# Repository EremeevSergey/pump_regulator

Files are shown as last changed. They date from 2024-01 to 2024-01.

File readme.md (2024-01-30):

# Реле контроля уровня.
## Описание.

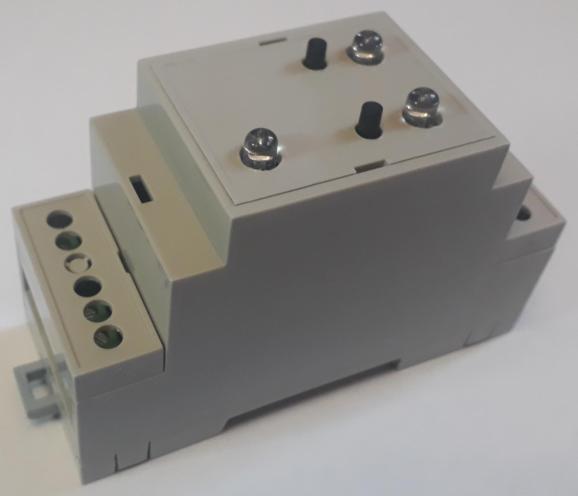
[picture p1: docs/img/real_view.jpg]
Внешний вид


Позволяет контролировать уровень жидкости (откачивать/закачивать). Для контроля используются датчики с ***сухим контактом***, например:

+ [Датчик уровня жидкости герконовый](https://market.yandex.ru/product--poplavkovyi-vykliuchatel-priamoi/1811578569?sku=101921281993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)
+ [Поплавковый герконовый датчик уровня воды](https://www.ozon.ru/product/liquid-level-switch-m15-poplavkovyy-gerkonovyy-datchik-urovnya-vody-zhidkosti-rezba-m15-kabel-688831200/)
+ [Поплавковый выключатель, контроль уровня воды]( https://market.yandex.ru/product--poplavkovyi-vykliuchatel-priamoi/1811578569?sku=101921281993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)

Можно использовать нормально разомкнутые, нормально замкнутые контакты, а также и те и другие одновременно  (программируется каждый контакт индивидуально). Выход Реле имеет контакт нормально-замкнутый и нормально-разомкнутые контакты. 

Изначально Реле (устройство) разрабатывалось для откачки воды, но оно может быть использовано и для наполнения воды.

## Органы управления и индикации.
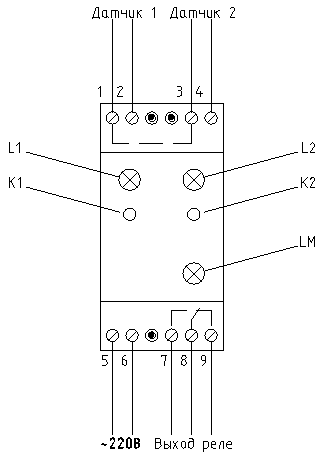
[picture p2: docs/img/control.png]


**Назначение клемм указано на рисунке.** Следует отметить, что клеммы 1, 3 внутри соединены между собой.

**L1, L2 - светодиоды, показывающие состояния датчиков (1 и 2 соответственно)**

| Цвет светодиода  | Описание |
|---|---|
| Красный | Датчик сработал |
| Зеленый | Датчик не сработал (контакт нормально-разомкнутый), т.е. контакт разомкнут.|
| Синий | Датчик не сработал (контакт нормально-замкнутые), т.е. контакт замкнут |

**K1, K2 - кнопки управления**

Долгое нажатие (10 сек. и дольше) на одну из кнопок переключает тип датчика с нормально-разомкнутого на нормально-замкнутый и наоборот. Тип датчика сохраняется даже после отключения питания. Для нормально-разомкнутого контакта в несработанном состоянии светодиод горит Зеленым цветом, а для нормально-замкнутого - Синим.

Если нажать и удерживать (10 сек. и дольше) одновременно две кнопки, то Реле переключиться с автоматического на ручной режима работы (и наоборот).
При переходе в ручной режим работы выход Реле отключается. Режим работы не запоминается и при включении, всегда устанавливается автоматический режим.

В ручном режиме работы кнопка K1 включает выходное Реле, а кнопка K2 - выключает. Для возврата в автоматический режим надо либо отключить питание (секунды на 2-3) либо нажать и удерживать (10 сек. и дольше) одновременно две кнопки K1 и K2. 

**LM - светодиод состояния выходного реле**
| Цвет светодиода  | Описание |
|---|---|
| Красный горит | Выходного реле включено |
| Зеленый горит | Выходного реле (автоматический режим работы) |
| Синий горит | Выходного реле (ручной режим работы) |

Если светодиод моргает (не важно каким цветом), значит Реле не смогло правильно прочитать из внутренней памяти (или записать в память) тип датчика. В этом случае тип всех контактов всегда будет нормально-разомкнутым. Вообще такое вряд-ли может случиться, т.к. ресурс флэш-памяти микроконтроллера реле позволят записывать не менее 100 000 раз. Чтобы затереть ячейки флэш-памяти надо будет очень часто менять типы контактов датчиков.

## Подключение.
### Откачиваем воду.
Схема подключения приведена ниже.
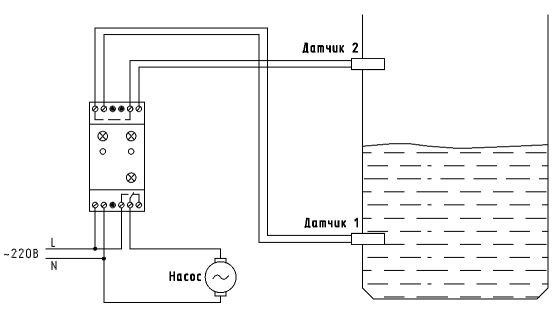
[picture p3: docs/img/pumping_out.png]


Самый правильный вариант, это поставить нормально-разомкнутые контакты (Датчик 1 и Датчик 2). В данном случае насос будет включаться только когда уровень воды поднимется выше Датчика 2 и будет откачивать воду пока её уровень не опустится ниже Датчика 1, или пропадёт напряжение питания (после восстановления питания, откачка воды возобновиться только, когда уровень воды опять поднимется выше датчика 2).

Если нет нормально-разомкнутых датчиков, можно поставить и нормально-замкнутые. В это случае надо будет кнопками К1, К2 поменять тип датчика (см. выше). 

### Набираем воду.

Как упоминалось в начале, Реле изначально разрабатывалось для откачки воды. Поэтому для обеспечения наборы воды есть несколько вариантов, каждый из которых имеет нюансы:

1. Назовём этот вариант "агрессивный". Т.е., если при включении  уровень воды будет ниже Датчика 2, насос включится и будет работать пока не "докачает" воду до Датчика 2. Далее он выключиться до тех пор пока уровень воды не спадёт до уровня Датчика 1. 

Подключение аналогично схеме "откачки воды", только насос подключаем к замкнутому выходному контакту Реле а не к разомкнутому.

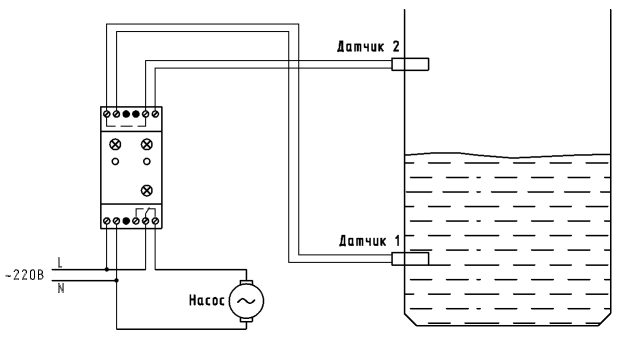
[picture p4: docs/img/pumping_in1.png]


Этот вариант меня смущает тем, что мы подключаем насос к нормально-замкнутым выходным контактам (см. схему). Вроде и ничего, но .... а вдруг Реле "сдохнет". Тогда с большей вероятностью выход отключиться, но т.к. насос подключен к нормаль-замкнутым контактам, он будет работать, пока мы его из сети не выключим.

2. Назовём это вариант "ленивый".
В данном варианте мы меняем местами датчики, и кнопками "инвертируем" состояния датчиков (программируем, см. выше), т.е. если у нас стоят нормально-разомкнутые контакты, мы их переводим в режим нормально-замкнутых, и наоборот. Насос подключаем через нормально-разомкнутые контакты Реле (как и при откачки воды).

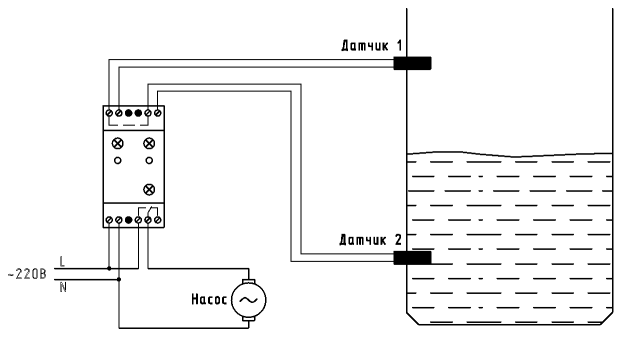
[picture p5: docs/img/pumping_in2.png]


При такой схеме включения насос будет включаться только, если уровень воды опуститься ниже Датчика 2, и работать до тех пор, пока уровень воды не достигнет Датчика 1. Здесь у нас нет минуса первого варианта, но то, что мы меняем тип контакта, возможно может сбить с толку. Мне данный вариант кажется более надежным и оптимальным.

[Кое-что про изготовление](docs/build.md)

[Для тех, кто будет переделывать (дорабатывать)](docs/info.md)

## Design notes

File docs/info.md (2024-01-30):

# Для тех, кто решит что-либо переделать.
## Программы

Я использовал:
1. [Kicad](https://www.kicad.org/download/) для разработки схем и печатных плат.
2. [Eclipse](https://www.eclipse.org/downloads/packages/release/2023-12/r/eclipse-ide-embedded-cc-developers) для отладки (разработки) прошивки микроконтроллера
3. [OpenOCD](https://github.com/openocd-org/openocd/releases/download/v0.12.0/openocd-v0.12.0-i686-w64-mingw32.tar.gz)  для программирование микроконтроллера и отладки
4. Qt Creator  и Qt 5.15.XX для написания эмулятора насосной станции и основной части прошивки (не зависящей от используемого микроконтроллера, да и системы вообще).

Думаю для пользователей Linux-ов не возникнет проблем с установкой этих программ. В Debian я всё за исключением Eclipse устанавливал пакетным менеджером. Eclipse скачивал с официального сайта.

А вот пользователи Windows могут столкнутся с проблемами при скачивании Qt Creator  и Qt 5.15.XX. Нехорошие люди не дают скачивать инсталяторы с официального сайта Россиянам. Мне не помогли даже танцы с бубном... Но если не использовать эмулятор, то и не надо будет всё это скачивать.

## Структура каталогов
```
./
 +-- case                      - документация на корпус
 +-- docs                      - то что мы сейчас читаем
 +-- firmware                  - проект Eclipse прошивки микроконтроллера
 |   +-- release/stm32f030f4p6 - сама прошивка
 |   +-- src/system            - не зависимый от платформы исходный код прошивки
 |   |   +-- config.h          - настроечные константы прошивки
 |   |   +-- hw_specific.h     - предварительные объявления функций, зависящих от платформы
 |   |   |   ...
 |   |      
 |   +-- stm32f030f4p6         - код пошивки для MCU stm32f030f4p6
 |       +-- eeprom            - "драйвер" виртуального EEPROM
 |       |   ...               - всё, что касается stm32f030f4p6
 |       
 +-- kicad
 |   +-- mcu/stm32f030f4p6     - проект Kicad платы микроконтроллера
 |   +-- power                 - проект Kicad силовой платы 
 |
 +-- simulator                 - прокт Qt Creator эмулятора
 ```
 
## Железо
Я использую Kicad, т.к. я нищеброд, и денег на платный софт у меня нет. А Kicad перекрывает все мои потребности, бесплатный, развивающийся и работает на всех системах (Linux, Windows, macOS).

Проекты Kicad-а лежат в отдельных папках  [Силовая плата](../kicad/power/), [Плата микроконтроллера](../kicad/mcu/stm32f030f4p6/)

## Прошивка
Основной код системы лежит в [firmware/src/system/](../firmware/src/system/). Он же используется и в эмуляторе, т.е. его напрямую там можно отладить. 

Файл "config.h" содержит настроечные константы (делители для таймеров) а также описаны используемые ножки микроконтроллера. Файл "hw_specific.h" содержит объявления функция зависящих от оборудования. Определения этих функций содержатся для stm32f030f4p6 в [hw_specific.cpp](../firmware/stm32f030f4p6/hw_specific.cpp), а для эмулятора в [simulator.cpp](../simulator/simulator.cpp).

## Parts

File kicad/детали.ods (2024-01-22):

Collated Components:
Item | Qty | Reference(s) | Value | LibPart | Цена | Стоимость | Магазин |  | Цена | Стоимость | Магазин
1 | 1 | BD1 | MB10F | диоды:MB10F | 4 | 4 | https://www.chipdip.ru/product/mb10f-hottech |  | 4 | 4 | https://www.chipdip.ru/product/mb10f-hottech
2 | 1 | C1 | C_Polarized_Small | Device:C_Polarized_Small | 18 | 18 | https://www.chipdip.ru/product0/9000565948 |  | 64 | 64 | https://www.chipdip.ru/product0/9000565948
3 | 1 | D1 | M3 | Device:D | 4 | 4 | https://www.chipdip.ru/product/m3-sunmate |  | 4 | 4 | https://www.chipdip.ru/product/m3-sunmate
4 | 1 | J1 | Conn_01x05 | Connector_Generic:Conn_01x05 | 2,6 | 2,6 | https://aliexpress.ru/item/32701800317.html?sku_id=61026197686 |  | 2,6 | 2,6 | https://aliexpress.ru/item/32701800317.html?sku_id=61026197686
5 | 1 | K1 | Реле_2-3 | реле:Реле_2-3 | 37 | 37 | https://aliexpress.ru/item/1005001994042589.html?sku_id=12000036214239182 |  | 42 | 42 | https://www.chipdip.ru/product0/8003916358
6 | 3 | P1, P3, P4 | CONN_2 | разъемы:CONN_2 | 12,7 | 38,1 | https://aliexpress.ru/item/32979388954.html?sku_id=66712511350 |  | 12,7 | 38,1 | https://aliexpress.ru/item/32979388954.html?sku_id=66712511350
7 | 1 | P2 | CONN_3 | разъемы:CONN_3 | 14,1 | 14,1 | https://aliexpress.ru/item/32979388954.html?sku_id=66712511351 |  | 14,1 | 14,1 | https://aliexpress.ru/item/32979388954.html?sku_id=66712511351
8 | 1 | T1 | Transformer_1P_1S | Device:Transformer_1P_1S | 540 | 540 | https://www.chipdip.ru/product0/8010765635 | https://www.chipdip.ru/product/tp112-k56 | 550 | 550 | https://www.chipdip.ru/product/tp112-k56
 | 1 | Печатная плата |  | (10 шт) | 290 | 290 |  |  | 600 | 600
Item | Qty | Reference(s) | Value | LibPart
1 | 2 | C1, C2 | C | Device:C | 2 | 4 |  |  |  | 0
2 | 1 | C3 | C_Polarized | Device:C_Polarized | 2 | 2 |  |  |  | 0
3 | 3 | D1, D2, D3 | LED_RKGB | Device:LED_RKGB | 8,8 | 26,4 | https://aliexpress.ru/item/32601543257.html?sku_id=65508728438 |  | 80 | 240 | https://www.chipdip.ru/product0/8413660661
4 | 1 | J1 | Conn_01x05 | Connector_Generic:Conn_01x05 | 2,6 | 2,6 | https://aliexpress.ru/item/32701800317.html?sku_id=61026197686 |  | 2,6 | 2,6 | https://aliexpress.ru/item/32701800317.html?sku_id=61026197686
5 | 1 | J2 | Conn_01x04 | Connector_Generic:Conn_01x04 | 2 | 2 | https://aliexpress.ru/item/32701800317.html?sku_id=61026197685 |  | 2 | 2 | https://aliexpress.ru/item/32701800317.html?sku_id=61026197685
6 | 2 | PB1, PB2 | кнопка | кнопки:кнопка | 6,05 | 12,1 | https://aliexpress.ru/item/1005004254514071.html?sku_id=12000028534796959 |  | 9 | 18 | https://www.chipdip.ru/product/kls7-ts6601-11.0-180-it-1102k
7 | 1 | Q1 | BC817 | Device:Q_NPN_BEC | 4 | 4 | https://www.chipdip.ru/product/bc817-16-hottech |  | 4 | 4 | https://www.chipdip.ru/product/bc817-16-hottech
8 | 1 | R1 | R | Device:R | 0,5 | 0,5 | https://aliexpress.ru/item/1005001794416354.html?sku_id=12000017596091305 |  | 0,5 | 0,5 | https://aliexpress.ru/item/1005001794416354.html?sku_id=12000017596091305
9 | 3 | R2, R5, R8 | 104 | Device:R | 0,5 | 1,5 | https://aliexpress.ru/item/1005001794416354.html?sku_id=12000017596091305 |  | 0,5 | 1,5 | https://aliexpress.ru/item/1005001794416354.html?sku_id=12000017596091305
10 | 4 | R3, R6, R9, R10 | 224 | Device:R | 0,5 | 2 | https://aliexpress.ru/item/1005001794416354.html?sku_id=12000017596091305 |  | 0,5 | 2 | https://aliexpress.ru/item/1005001794416354.html?sku_id=12000017596091305
11 | 2 | R4, R7 | 64 | Device:R | 0,5 | 1 | https://aliexpress.ru/item/1005001794416354.html?sku_id=12000017596091305 |  | 0,5 | 1 | https://aliexpress.ru/item/1005001794416354.html?sku_id=12000017596091305
12 | 1 | U1 | AMS1117-3.3 | Regulator_Linear:AMS1117-3.3 | 9 | 9 | https://www.chipdip.ru/product/ams1117-3.3-umw |  | 9 | 9 | https://www.chipdip.ru/product/ams1117-3.3-umw
13 | 1 | U2 | STM32F030F4Px | MCU_ST_STM32F0:STM32F030F4Px | 60,4 | 60,4 | https://aliexpress.ru/item/1005005652086561.html?sku_id=12000033892723179 |  | 190 | 190 | https://www.chipdip.ru/product/stm32f030f4p6
 | 1 | Печатная плата |  | (10 шт) | 338 | 338 |  |  | 600 | 600
 | 2 | Conn_01x05 | Мама |  | 1,6 | 3,2 | https://aliexpress.ru/item/32715864245.html?sku_id=61026413131 |  | 1,6 | 3,2 | https://aliexpress.ru/item/32715864245.html?sku_id=61026413131
 | 10 | Conn_01x05 | Контакты |  | 1,4 | 14 | https://aliexpress.ru/item/32690584570.html?sku_id=60493826630 |  | 1,4 | 14 | https://aliexpress.ru/item/32690584570.html?sku_id=60493826630
 | 1 | Корпус |  |  | 310 | 310 | https://meandr-shop.ru/korpus-141/ |  | 540 | 540 | https://www.chipdip.ru/product/d3mg
 |  |  |  |  |  | 1740,5 |  |  |  | 2946,6

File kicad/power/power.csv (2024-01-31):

Item | Qty | Reference(s) | Value | LibPart | Footprint | Datasheet | Qty | ChipDip | Цена | Стоимость | Aliexpress | Цена2 | Стоимость
1 | 1 | BD1 | MB10F | диоды:MB10F | диоды:MB-F |  | 1 | https://www.chipdip.ru/product/mb10f-hottech | 4 | 4 | https://aliexpress.ru/item/1005002106188652.html?sku_id=12000018760217218 | 4 | 4
2 | 1 | C1 | 1000x25V | Device:C_Polarized_Small | Capacitor_THT:CP_Radial_D10.0mm_P5.00mm | ~ | 1 | https://www.chipdip.ru/product0/9000565924 | 18 | 18 | https://www.chipdip.ru/product0/9000565924 | 18 | 18
3 | 2 | C2, C3 | ?? | Device:C_Small | Capacitor_SMD:C_1206_3216Metric | ~ | 2 |  |  | 0 |  |  | 0
4 | 5 | D1, D2, D3, D4, D5 | M1 | Device:D | Diode_SMD:D_SMA | ~ | 5 | https://www.chipdip.ru/product/m1-sunmate | 3 | 15 | https://aliexpress.ru/item/4000331358747.html?sku_id=10000001360601882 | 0,9 | 4,5
5 | 1 | J1 | Conn_01x05 | Connector_Generic:Conn_01x05 | Connector_JST:JST_EH_B5B-EH-A_1x05_P2.50mm_Vertical | ~ | 1 | https://aliexpress.ru/item/32701800317.html?sku_id=61026197686 | 3,2 | 3,2 | https://aliexpress.ru/item/32701800317.html?sku_id=61026197686 | 3,2 | 3,2
6 | 4 | JP1, JP2, JP3, JP4 | SolderJumper_2_Bridged | Jumper:SolderJumper_2_Bridged | Jumper:SolderJumper-2_P1.3mm_Bridged_Pad1.0x1.5mm | ~ | 4 |  | 0 | 0 |  | 0 | 0
7 | 1 | K1 | SRD-12VDC-SL-C | реле:Реле_2-3 | реле:SRD-12VDC-SL-C | https://oskolchip.ru/datasheet/SRD-05-12-24VDC-SL-C.pdf | 1 | https://www.chipdip.ru/product0/8023333076 | 60 | 60 | https://aliexpress.ru/item/1005001994042589.html?sku_id=12000036214239182 | 37 | 37
8 | 3 | P1, P3, P4 | CONN_2 | разъемы:CONN_2 | разъемы:KF128-2P |  | 3 | https://www.chipdip.ru/product/dg500-5.08-02p-14-00ah | 38 | 114 | https://aliexpress.ru/item/32979388954.html?sku_id=66712511350 | 13,3 | 39,9
9 | 1 | P2 | CONN_3 | разъемы:CONN_3 | разъемы:KF128-3P |  | 1 | https://www.chipdip.ru/product/dg500-5.08-03p-14-00a-h | 42 | 42 | https://aliexpress.ru/item/32979388954.html?sku_id=66712511351 | 14,6 | 14,6
10 | 1 | TR1 | ТПК-1 (9В, 0.17А ) | Transformer:TEZ2.0-D-1 | трансформаторы:ТПК-1 | http://www.breve.pl/pdf/ANG/TEZ_ang.pdf | 1 | https://www.chipdip.ru/product/tpk-1-9v | 540 | 540 | https://www.chipdip.ru/product0/8010765633 | 320 | 320
 |  |  |  |  |  |  |  |  |  | 796,2 |  |  | 441,2

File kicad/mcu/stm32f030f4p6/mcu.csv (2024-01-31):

Item | Qty | Reference(s) | Value | ChipDip | Цена | Стоимость | Aliexpress | Цена 2 | Стоимость
1 | 4 | C1, C2, C4, C5 | 0.1 | https://www.chipdip.ru/product0/9000649656 | 6 | 24 | https://www.chipdip.ru/product0/9000649656 | 6 | 24
2 | 2 | C3, C6 | 100.0x6.3V | https://www.chipdip.ru/product/tecap-100-mkf-6.3-v-tip-c-10 | 31 | 62 | https://www.chipdip.ru/product/tecap-100-mkf-6.3-v-tip-c-10 | 31 | 62
3 | 3 | D1, D2, D3 | LED_RKGB | https://aliexpress.ru/item/1005004567358995.html?sku_id=12000029654169026 | 14 | 42 | https://aliexpress.ru/item/1005004567358995.html?sku_id=12000029654169026 | 14 | 42
4 | 1 | J1 | Conn_01x05 | https://aliexpress.ru/item/1005004837211340.html?sku_id=12000030681544706 | 32 | 32 | https://aliexpress.ru/item/1005004837211340.html?sku_id=12000030681544706 | 32 | 32
5 | 1 | J2 | SWD |  | 0 | 0 |  | 0 | 0
6 | 2 | PB1, PB2 | кнопка | https://www.chipdip.ru/product/kls7-ts6601-11.0-180-it-1102k | 9 | 18 | https://www.chipdip.ru/product/kls7-ts6601-11.0-180-it-1102k | 9 | 18
7 | 1 | PB3 | Reset |  | 0 | 0 |  | 0 | 0
8 | 1 | Q1 | BC817 | https://www.chipdip.ru/product/bc817-16-hottech | 4 | 4 | https://www.chipdip.ru/product/bc817-16-hottech | 4 | 4
9 | 1 | R1 | 10k | https://aliexpress.ru/item/1005001794416354.html?sku_id=12000017596091297 | 0,47 | 0,47 | https://aliexpress.ru/item/1005001794416354.html?sku_id=12000017596091297 | 0,47 | 0,47
10 | 3 | R2, R5, R8 | 100 | https://aliexpress.ru/item/1005001794416354.html?sku_id=12000017596091249 | 0,47 | 1,41 | https://aliexpress.ru/item/1005001794416354.html?sku_id=12000017596091249 | 0,47 | 1,41
11 | 3 | R3, R6, R9 | 220 | https://aliexpress.ru/item/1005001794416354.html?sku_id=12000017596091257 | 0,47 | 1,41 | https://aliexpress.ru/item/1005001794416354.html?sku_id=12000017596091257 | 0,47 | 1,41
12 | 3 | R4, R7, R11 | 62 | https://aliexpress.ru/item/1005001794416354.html?sku_id=12000017596091244 | 0,47 | 1,41 | https://aliexpress.ru/item/1005001794416354.html?sku_id=12000017596091244 | 0,47 | 1,41
13 | 1 | R10 | 1k | https://aliexpress.ru/item/1005001794416354.html?sku_id=12000017596091273 | 0,47 | 0,47 | https://aliexpress.ru/item/1005001794416354.html?sku_id=12000017596091273 | 0,47 | 0,47
14 | 1 | U1 | LM1117-3.3 | https://www.chipdip.ru/product/lm1117gs-3.3 | 21 | 21 | https://www.chipdip.ru/product/lm1117gs-3.3 | 21 | 21
15 | 1 | U2 | STM32F030F4P6 | https://www.chipdip.ru/product/stm32f030f4p6tr-2?from=suggest_product | 100 | 100 | https://aliexpress.ru/item/1005006074715370.html?sku_id=12000035611654155 | 80 | 80
 |  |  |  |  |  | 308,17 |  |  | 288,17

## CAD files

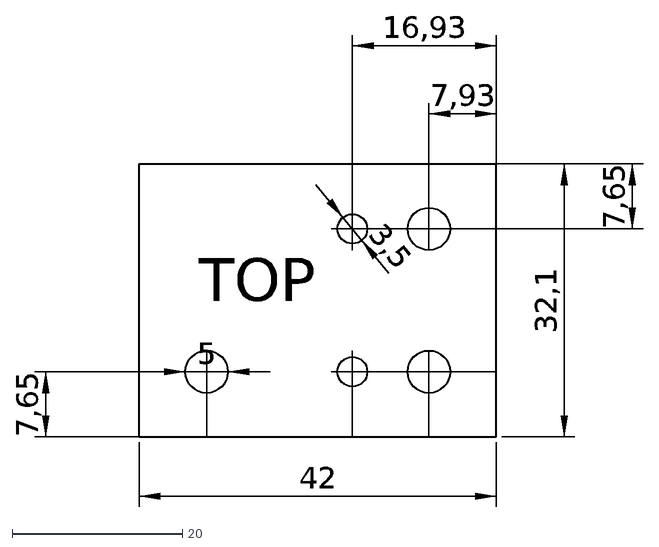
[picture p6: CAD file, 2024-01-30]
case/front_panel.dxf
42
32,1
5
3,5
TOP
7,65
7,93
16,93

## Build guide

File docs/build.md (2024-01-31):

# Замечания по изготовлению.

Вообще-то минимальный необходимый функционал можно сделать на обычном реле с двумя группами контактов, и скорее всего это будет дешевле. Но вдруг, кто-то решит это повторить.... 

## Платы.

Платы (две штуки) рисовались в [Kicade](https://www.kicad.org/). Программа доступна бесплатно для скачивания и есть для Widows, Linux и вроде для iOs (не проверял - не знаю). 

К сожалению все платы двухсторонние, но ели руки растут откуда надо, то их можно и ЛУТом сделать (я так и делал). Если будете заказывать у "друзей" на производстве, то необходимые файлы для платы блока питания лежат [тут](kicad/power/gerber/), а для платы микроконтроллера [тут](kicad/mcu/stm32f030f4p6/gerber/).

Kicad лучше поставить, чтобы видеть куда какие детали впаивать. Из него же можно сделать и все необходимые файлы для изготовления плат.

### Стоимость
По стоимости, точно сложно сказать. Всё зависит от объёмов и где покупать детали. Если покупать детали в Чипе-Дипе и заказывать платы в Резоните, то цена может достичь 2500-3000 рублей. Если делать хотя-бы штук 5 и всё брать (детали и платы) в Китае (тот-же Алиэкспрес), то думаю до 1500 руб цену можно снизить. Правда стоит учитывать, что тот же Али продаёт не по 1 штуке, а по 10, 50, 100 шт.

Я потратил на изготовление 962 руб. При этом у меня была почти вся мелочевка, включая микроконтроллер, разъёмы и светодиоды. Трансформатор и корпус стоили 850 руб, т.е. почти 90 процентов затрат.

Список деталей (без учета самих плат и корпуса) можно посмотреть здесь ([силовая плата](../kicad/power/power.csv), [плата микроконтроллера](../kicad/mcu/stm32f030f4p6/mcu.csv)) или в Kicad-е.

### Силовая плата
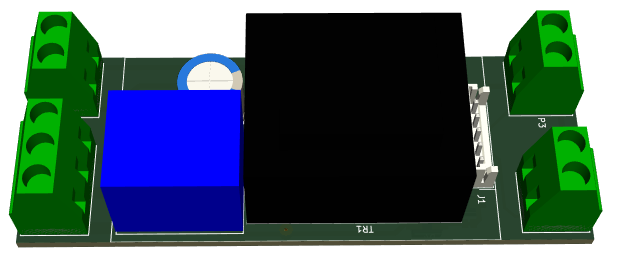
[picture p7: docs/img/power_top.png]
 
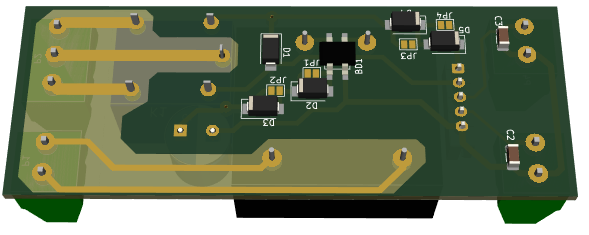
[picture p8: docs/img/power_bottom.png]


Блок питания не стабилизированный - обычный выпрямитель. На схеме есть 4 диода (D2-D5). Они на самом деле сделаны на всякий случай, если трансформатор будет выдавать большое (относительно) напряжение. Ими можно  вольта на два понизить напряжение. На плате они зашунтированы перемычками. Если диоды понадобятся, то перемычки надо будет разрезать. Конденсаторы С2, С3 я тоже на всякий случай поставил, сам я их не впаивал.

Мой экземпляр трансформатора выдавал на холостом ходу 16,7В, а под нагрузкой - 12-13В.

Всё устройство потребляет порядка от выпрямителя 60-70 мА. (30 мА реле и 30 мА плата микроконтроллера)

### Плата микроконтроллера
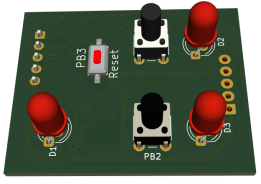
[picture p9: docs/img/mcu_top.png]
 
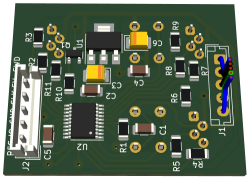
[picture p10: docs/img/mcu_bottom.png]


Кнопка "Reset" нужна только для того, чтобы ПЕРЕпрограммировать микроконтроллер. Ножек микросхемы не хватило, пришлось использовать оду из SWD. Поэтому раз запрограммировав, второй раз можно будет только замкнув Reset во время прошивки.
Вообще я вывел на разъём программирования вход Reset микроконтроллера. Если у программатора есть такой выход и он им пользуется, то вполне возможно, что с перепрограммирование проблем не возникнет. В любом случае кнопку эту можно не впаивать, а если приспичет, замкнуть её контактные площадки, например пинцетом.

В J1 (типа разъём) впаиваем просто провода. Если впаять разъём, то он упрётся в трансформатор на силовой плате и не даст закрыть корпус.

Я паял сначала все SMD, потом переходные отверстия, а потом уже всё выводное. Кнопки брал 13 мм высотой (выступают над передней панелью на 4 мм). Если буду делать ещё, возьму высотой [11 мм](https://www.chipdip.ru/product/kls7-ts6601-11.0-180-it-1102k)

Для программирование микроконтроллера придётся найти программатор ST-Link. Оказыается их много продаётся даже на Озоне ([Первый попавшийся](https://www.ozon.ru/product/programmator-st-link-stlink-st-link-v2-dlya-stm32-i-stm8-s-kryshkoy-i-kabelem-831963679/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программатор+st-link+v2))
, и даже недорого. Естественно за их работоспособность я не ручаюсь. Сам покупал лет 10 назад на Алиэкспресе. 

#### Программирование микроконтроллера
##### Linux (Debian, Ubunta и другие debian-based)
Используем OpenOCD.
```
sudo apt install openocd
```
заходим в [каталог с прошивкой](../firmware/release/stm32f030f4p6/) и даём команду:
```
openocd -f interface/stlink-v2.cfg -f target/stm32f0x.cfg -c "program pump_regulator.hex verify reset" -c "shutdown"
```
На других линуксах, как-то наподобие (главное openocd поставить).

Если надо будет повторно перепрошить микроконтроллер, то нажимаем кнопу Reset (замыкаем её контакты), запускаем команду openocd.... и отпускаем кнопку. Всё должно перепрошиться.

##### Windows
У ST есть [утилиты](https://www.st.com/en/development-tools/stsw-link004.html). Правда эти не хорошие люди видимо блокируют российские IP адреса. Мне просто так скачать не дали. Наверное лучше тоже установить 
[OpenOCD](https://github.com/openocd-org/openocd/releases/download/v0.12.0/openocd-v0.12.0-i686-w64-mingw32.tar.gz), а дальше аналогично Linux.

##### macOS
Понятия не имею, скорее всего аналогично Windows.

## Корпус
Корпус Gainta D2MG (ширина 2 модуля) покупал в [ЧипеДипе](https://www.chipdip.ru/product/d2mg?from=suggest_product). Как ни странно, с учетом доставки у них оказалось дешевле всего. Есть ещё 2-х модульный корпус у [Миландра](https://meandr-shop.ru/korpus-082/), но у него не предусмотрено крепление дополнительных плат в верхней части, и с учетом доставки для меня он оказался дороже (_вообще миландровцам стоит присмотреться к корпусам Gainta, они более функциональны_).

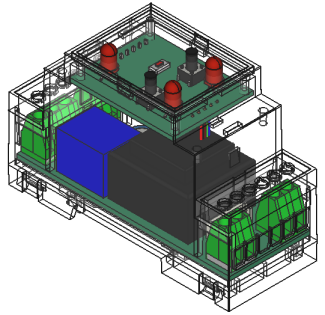
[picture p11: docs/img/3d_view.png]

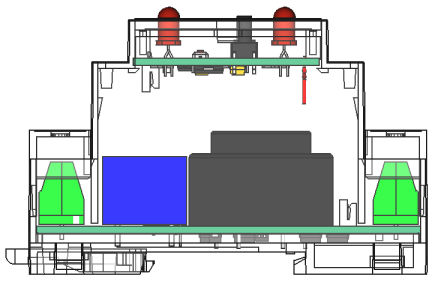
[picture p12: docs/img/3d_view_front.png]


В верхней крышке корпуса сверлим отверстия согласно [шаблона](../case/front_panel.pdf).

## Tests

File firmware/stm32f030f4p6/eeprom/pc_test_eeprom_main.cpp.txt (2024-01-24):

#include <cassert>
#include <iostream>
#include <algorithm>
#include <random>
#include <array>
using namespace std;
#include "src/flash_eeprom.h"

constexpr int TestArraySize = 1000'0000;
constexpr int PageSize      = 1024; // 1 кбайт
constexpr int PageCount     = 2; // 2 страницы
constexpr int Page0_Offset  = PageSize*14; // типа 14 кбайт
std::array<std::uint8_t,TestArraySize> testArray;
constexpr std::array<std::uint16_t,5> Addresses = {0x1122,0x3344,0x5566,0x7788,0x9900};
std::array<std::uint16_t,Addresses.size()> Values;
constexpr auto page0_address{testArray.data()+Page0_Offset};
CFlashEeprom<Addresses.size()+5> EEPROM(page0_address,PageSize);

std::uint16_t* toUint16Ptr(void* ptr){
    return static_cast<std::uint16_t*>(ptr);
}

int returnError(const char* str){
    std::cout << str << std::endl;
    return -1;
}

bool TestAllClear(){
    for (auto byte:testArray)
        if (byte!=0xFF) return false;
    return true;
}

/*!
 * \brief Проверям, что не вышли за пределы страниц виртуальной EEPROM
 * \return
 */
bool TestOutOfBounds(){
    for (int i=0;i<Page0_Offset;++i) if (testArray[i]!=0xFF) return false;
    for (int i=Page0_Offset+PageSize*PageCount;i<TestArraySize;++i) if (testArray[i]!=0xFF) return false;
    return true;
}

bool TestInitEeprom(){
    // Проверяем, что инициализация прошла успешно
    if (*toUint16Ptr(page0_address)!=0x0000) return false;
    if (*toUint16Ptr(page0_address+PageSize)!=0xFFFF) return false;
    return true;
}

int main()
{
    // Запоняем "флэш" FF
    for (auto& byte:testArray) byte = 0xFF;
    if (!TestAllClear()) return returnError("Что-то флешка срезу не чистая!?!?");
    EEPROM.Init();
    for (auto addr:Addresses) EEPROM.AddVirtualAddrress(addr);
    if (!TestOutOfBounds()) return returnError("Инициализация затерла другие страницы");
    if (!TestInitEeprom ()) return returnError("Инициализация прошла с ошибкой");
    // Теперь поназаписываем 1000 значний, и проверим, что последние записанные значения
    // правильно считываются
    std::mt19937  RndEngine_;
    std::uniform_int_distribution<std::uint16_t> distribution(0,0xFFFF);
    for (int i=0;i<1000000;++i){
        // Заполняем переменные случайными значениями
        for (auto& val: Values) val = distribution(RndEngine_);
        for (decltype(Addresses.size()) j=0;j<Addresses.size();++j){
            // Записываем и считываем
            if (EEPROM.WriteVariable(Addresses[j],Values[j])!=true){
                return returnError("Ошибка записи");
            }
            std::uint16_t data{0};
            if (EEPROM.ReadVariable(Addresses[j],data)!=true){
                return returnError("Ошибка чтения");
            }
            if (data!=Values[j]){
                return returnError("Считали не то, что записали");
            }
        }
    }
    if (!TestOutOfBounds()) return returnError("Затерли чужую память");
    std::cout << "All Ok." << std::endl;
    return 0;
}

void ErasePage(void* addr,int size){
    std::uint8_t* ptr = static_cast<std::uint8_t*>(addr);
    for (int i=0;i<size;++i) *(ptr+i) = 0xFF;
}

bool FLASH_ErasePage(void* addr){
    std::cout << "FLASH_ErasePage" << std::endl;
    ErasePage(addr,PageSize);
    return true;
}

bool FLASH_ProgramHalfWord(void* address,std::uint16_t data){
    std::uint16_t* ptr = static_cast<std::uint16_t*>(address);
    if ((*ptr)!=0xFFFF /*&& (*ptr)!=0xEEEE*/){
        std::cout << std::hex <<  "not FFFF "  << (*ptr) << std::endl;
        assert((*ptr)==0xEEEE);
    }
    *ptr = data;
    return true;
}

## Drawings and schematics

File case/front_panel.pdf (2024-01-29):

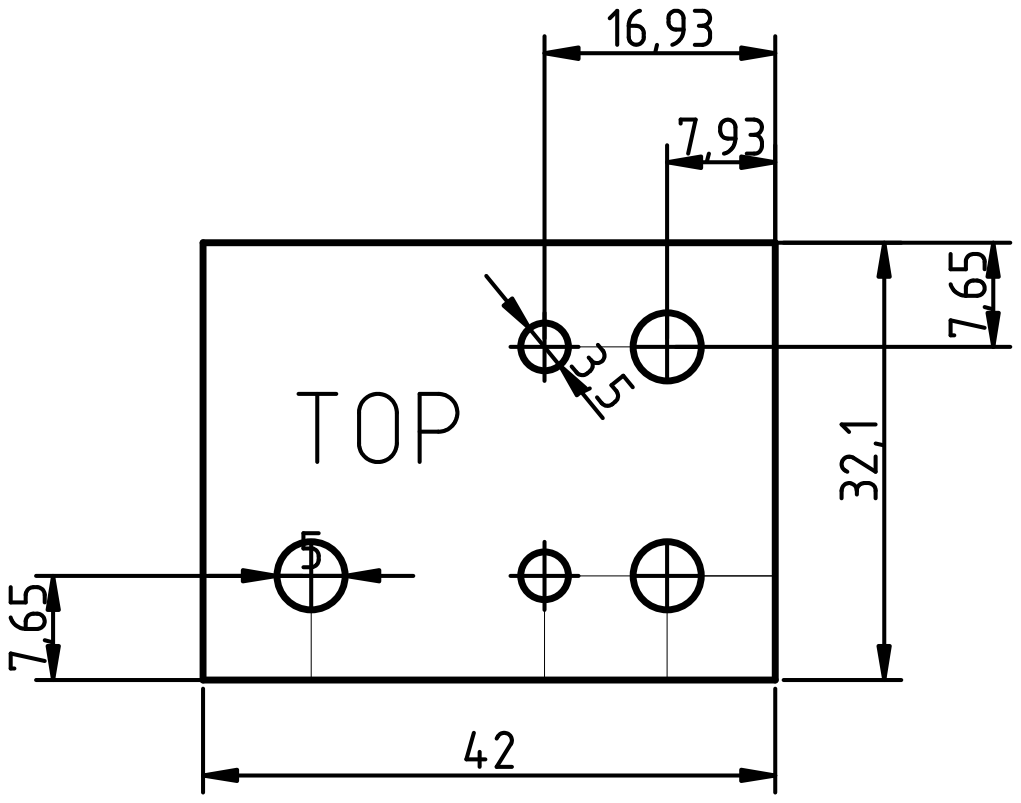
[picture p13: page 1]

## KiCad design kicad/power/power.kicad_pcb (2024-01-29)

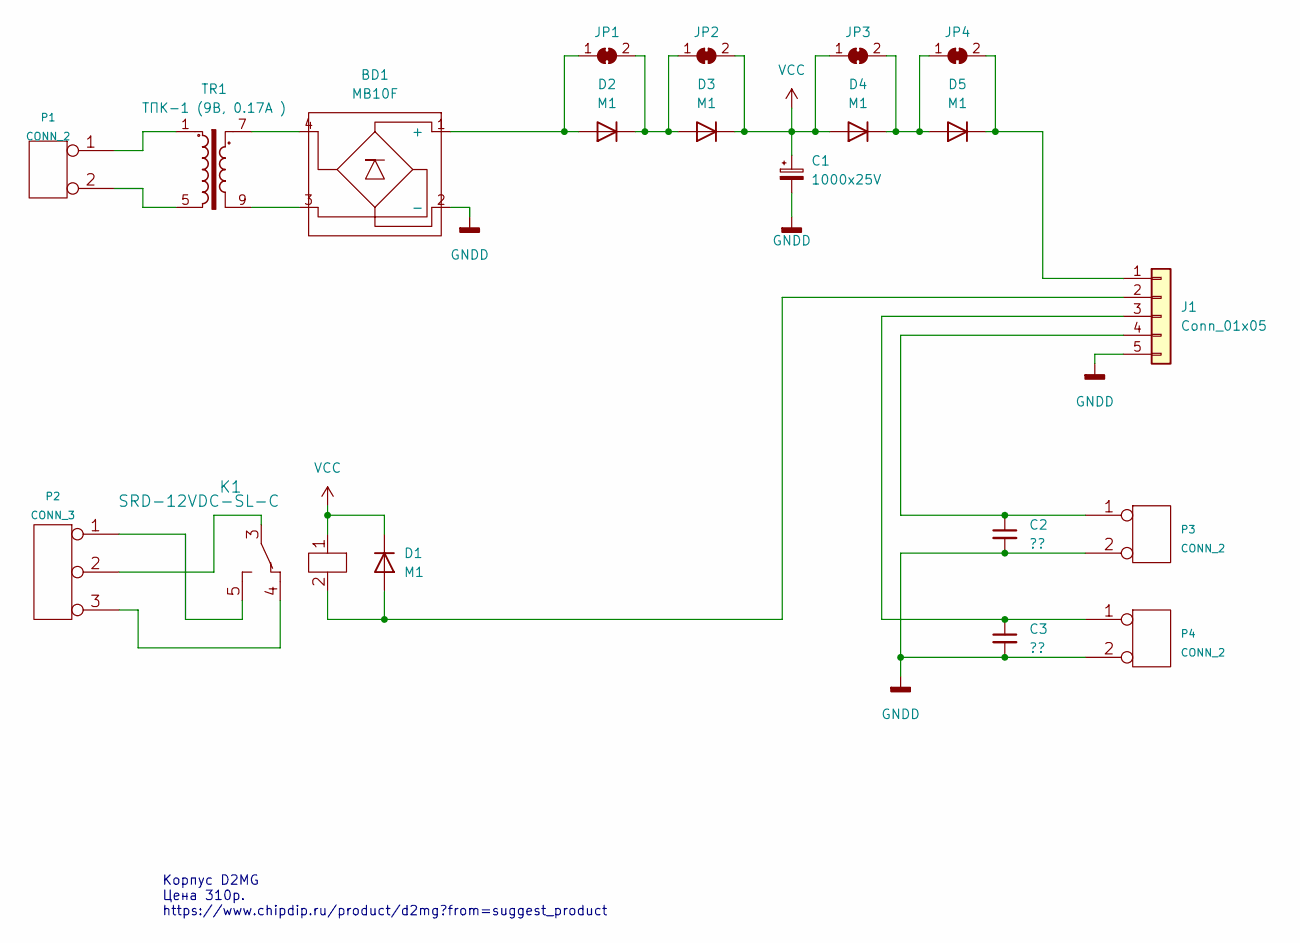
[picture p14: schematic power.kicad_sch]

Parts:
BD1: MB10F; MB-F
C1: 1000x25V; CP_Radial_D10.0mm_P5.00mm
C2, C3: ??; C_1206_3216Metric
D1, D2, D3, D4, D5: M1; D_SMA
J1: Conn_01x05; JST_EH_B5B-EH-A_1x05_P2.50mm_Vertical
JP1, JP2, JP3, JP4: SolderJumper_2_Bridged; SolderJumper-2_P1.3mm_Bridged_Pad1.0x1.5mm
K1: SRD-12VDC-SL-C
P1, P3, P4: CONN_2; KF128-2P
P2: CONN_3; KF128-3P
TR1: ТПК-1 (9В, 0.17А ); ТПК-1

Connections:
GNDD: BD1.2 (-), C1.2, C2.2, C3.2, J1.5, P3.2 (PM), P4.2 (PM)
unnamed: BD1.1 (+), D2.2 (A), JP1.1 (A)
unnamed: BD1.3, TR1.9
unnamed: BD1.4, TR1.7
unnamed: C2.1, J1.4, P3.1
unnamed: C3.1, J1.3, P4.1
unnamed: D1.2 (A), J1.2, K1.2 (in2)
unnamed: D2.1 (K), D3.2 (A), JP1.2 (B), JP2.1 (A)
unnamed: D4.1 (K), D5.2 (A), JP3.2 (B), JP4.1 (A)
unnamed: D5.1 (K), J1.1, JP4.2 (B)
unnamed: K1.3 (out2), P2.2
unnamed: K1.4 (out1), P2.3
unnamed: K1.5 (out3), P2.1
unnamed: P1.1, TR1.1
unnamed: P1.2 (PM), TR1.5
VCC: C1.1, D1.1 (K), D3.1 (K), D4.2 (A), JP2.2 (B), JP3.1 (A), K1.1 (in1)

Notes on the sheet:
Корпус D2MG Цена 310р. https://www.chipdip.ru/product/d2mg?from=suggest_product

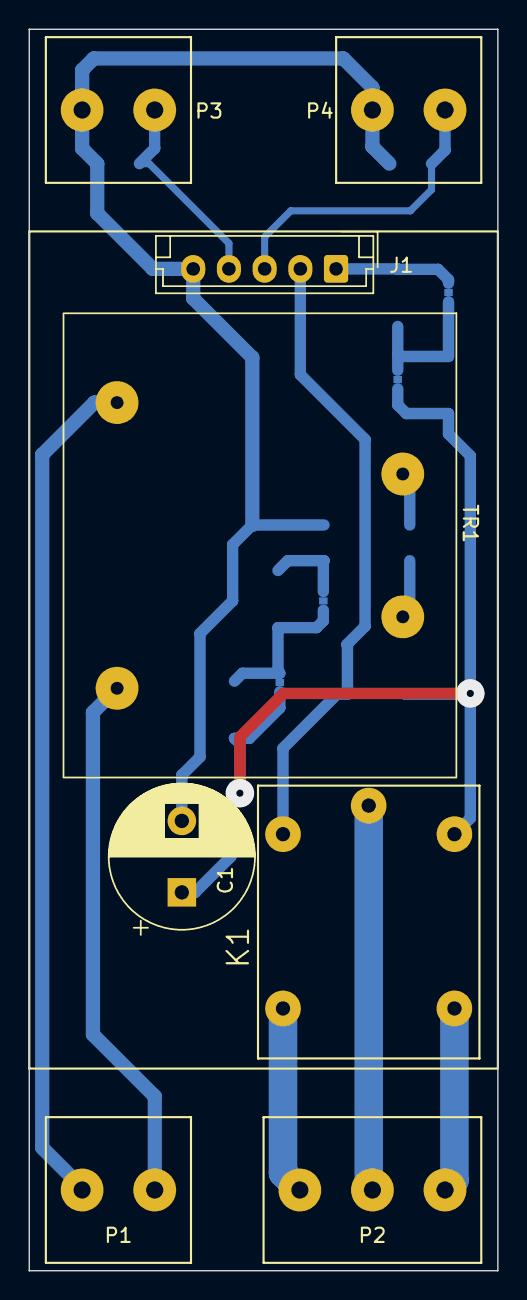
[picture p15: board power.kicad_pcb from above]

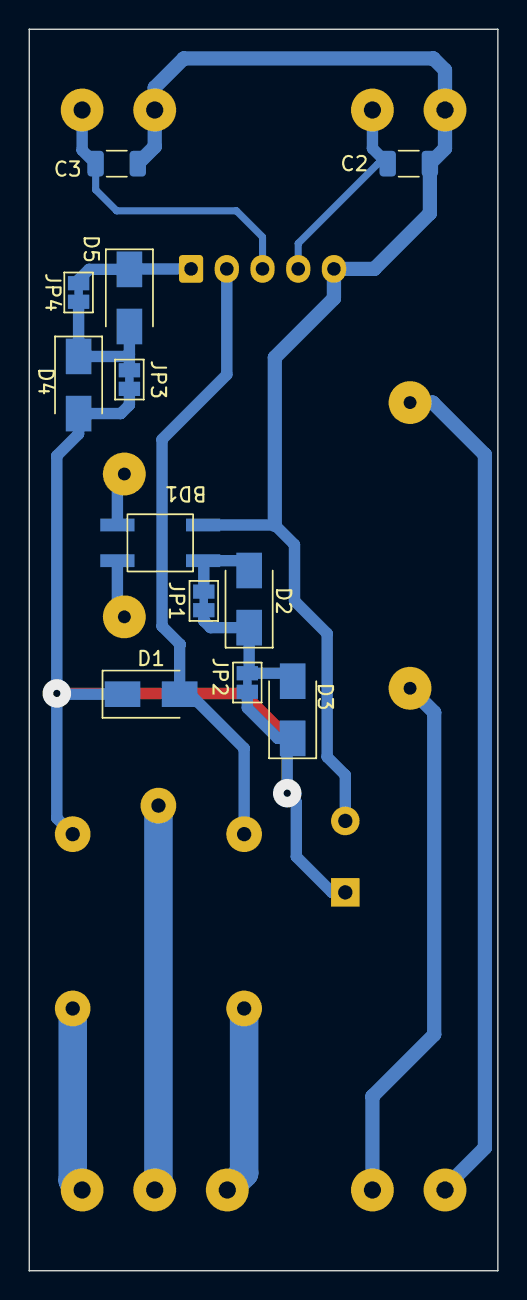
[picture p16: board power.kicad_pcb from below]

Board: 2 copper layers, 32.8 x 86.9 mm, 20 parts (12 on the bottom side), 16 nets.

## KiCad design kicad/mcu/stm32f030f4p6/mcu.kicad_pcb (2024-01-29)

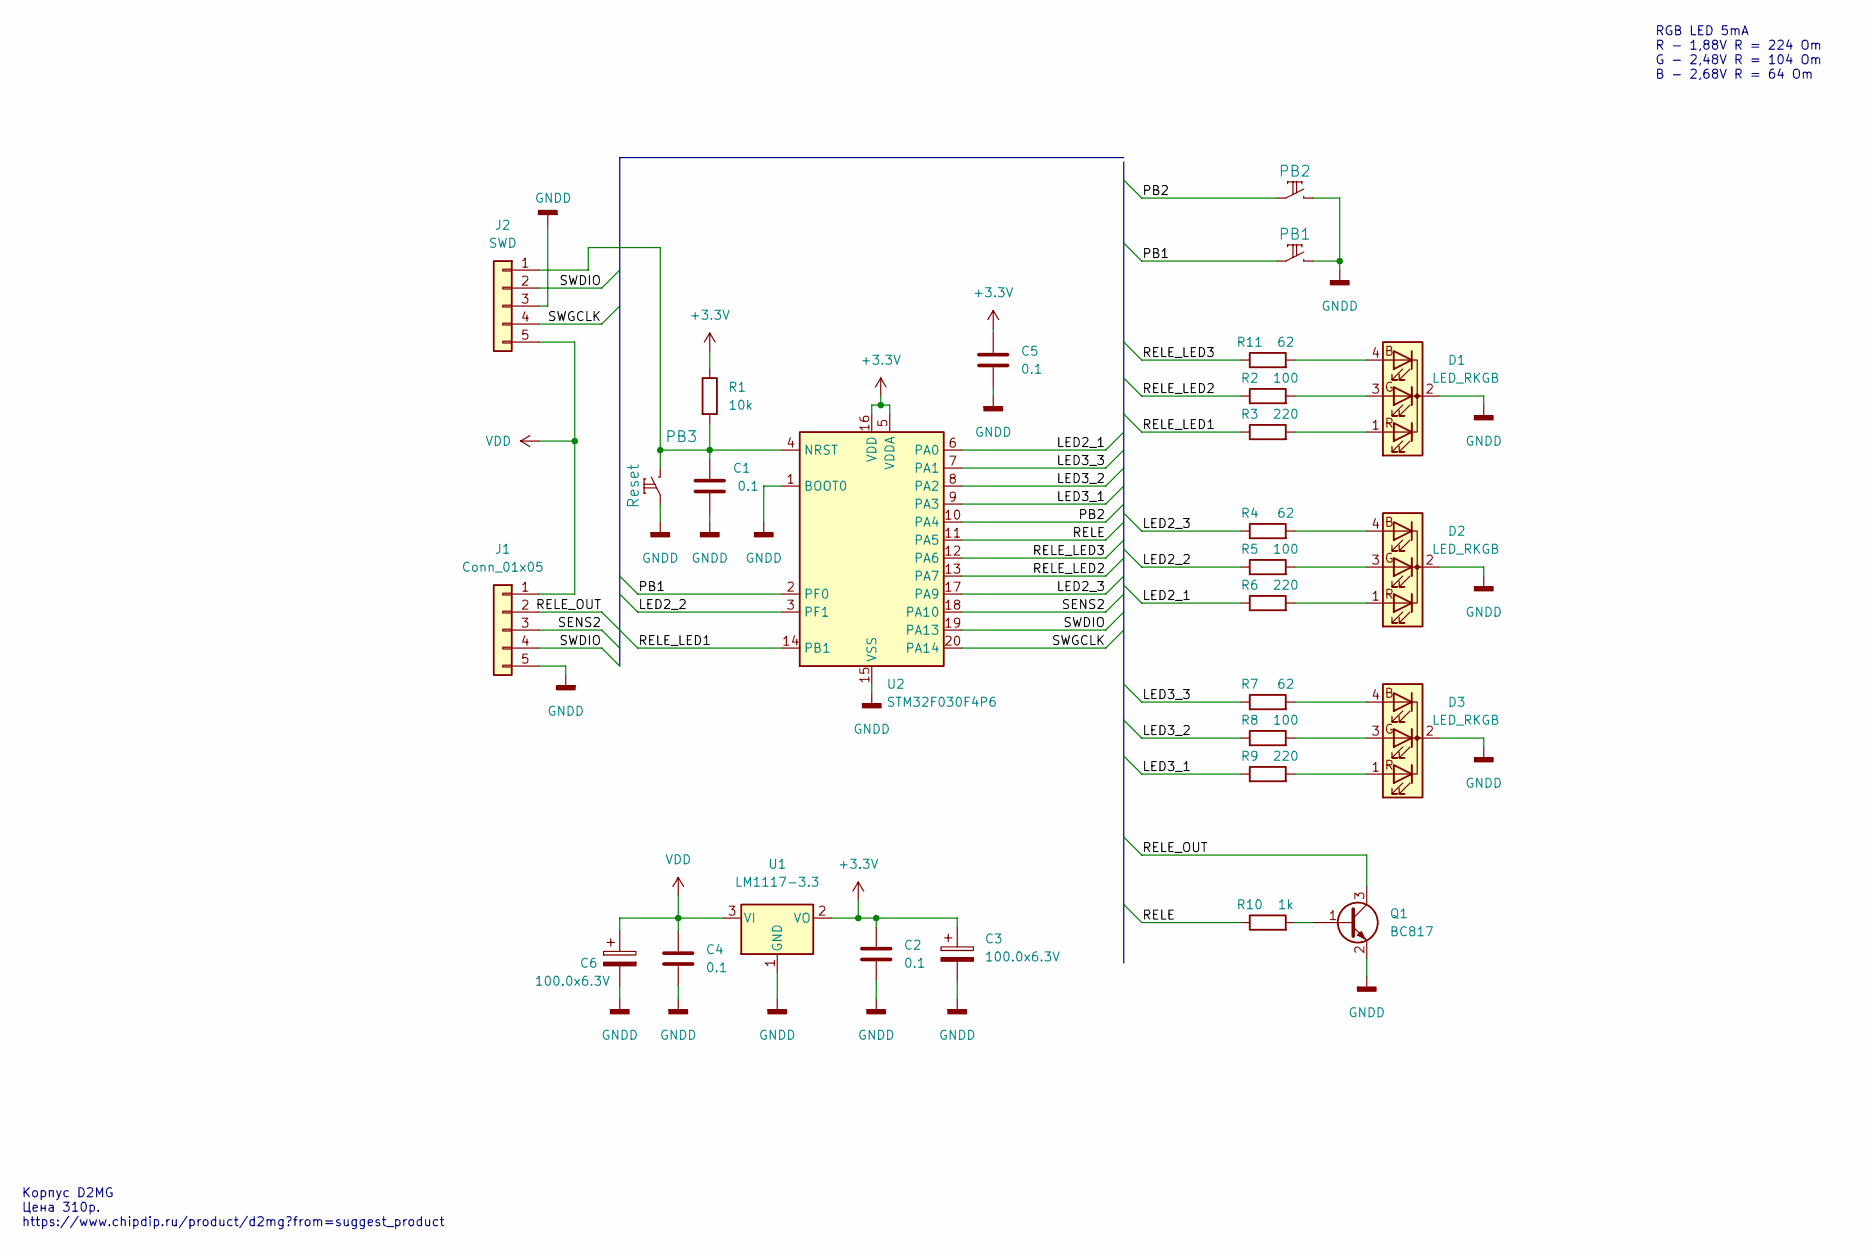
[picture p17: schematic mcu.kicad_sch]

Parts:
C1, C2, C4, C5: 0.1; C_1206_3216Metric
C3, C6: 100.0x6.3V; CP_EIA-3528-21_Kemet-B_Pad1.50x2.35mm_HandSolder
D1, D2, D3: LED_RKGB; LED_D5.0mm-4_RGB_Staggered_Pins
J1: Conn_01x05; JST_EH_B5B-EH-A_1x05_P2.50mm_Vertical
J2: SWD; JST_EH_B5B-EH-A_1x05_P2.50mm_Vertical
PB1, PB2: кнопка; SW_PUSH_6mm
PB3: Reset; PB_SMD_3x6x2.5
Q1: BC817; SOT-23
R1: 10k; R_1206_3216Metric
R2, R5, R8: 100; R_1206_3216Metric
R3, R6, R9: 220; R_1206_3216Metric
R4, R7, R11: 62; R_1206_3216Metric
R10: 1k; R_1206_3216Metric
U1: LM1117-3.3; SOT-223-3_TabPin2
U2: STM32F030F4P6; TSSOP-20_4.4x6.5mm_P0.65mm

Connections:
+3.3V: C2.1, C3.1, C5.1, R1.1, U1.2 (VO), U2.5 (VDDA), U2.16 (VDD)
/LED2_1: R6.1, U2.6 (PA0)
/LED2_2: R5.1, U2.3 (PF1)
/LED2_3: R4.1, U2.17 (PA9)
/LED3_1: R9.1, U2.9 (PA3)
/LED3_2: R8.1, U2.8 (PA2)
/LED3_3: R7.1, U2.7 (PA1)
/PB1: PB1.2, U2.2 (PF0)
/PB2: PB2.2, U2.10 (PA4)
/RELE: R10.1, U2.11 (PA5)
/RELE_LED1: R3.1, U2.14 (PB1)
/RELE_LED2: R2.1, U2.13 (PA7)
/RELE_LED3: R11.1, U2.12 (PA6)
/RELE_OUT: J1.2, Q1.3 (C)
/SENS2: J1.3, U2.18 (PA10)
/SWDIO: J1.4, J2.2, U2.19 (PA13)
/SWGCLK: J2.4, U2.20 (PA14)
GNDD: C1.1, C2.2, C3.2, C4.2, C5.2, C6.2, D1.2 (K), D2.2 (K), D3.2 (K), J1.5, J2.3, PB1.1, PB2.1, PB3.2, Q1.2 (E), U1.1 (GND), U2.1 (BOOT0), U2.15 (VSS)
unnamed: C1.2, J2.1, PB3.1, R1.2, U2.4 (NRST)
unnamed: D1.1 (RA), R3.2
unnamed: D1.3 (GA), R2.2
unnamed: D1.4 (BA), R11.2
unnamed: D2.1 (RA), R6.2
unnamed: D2.3 (GA), R5.2
unnamed: D2.4 (BA), R4.2
unnamed: D3.1 (RA), R9.2
unnamed: D3.3 (GA), R8.2
unnamed: D3.4 (BA), R7.2
unnamed: Q1.1 (B), R10.2
VDD: C4.1, C6.1, J1.1, J2.5, U1.3 (VI)

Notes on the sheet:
Корпус D2MG Цена 310р. https://www.chipdip.ru/product/d2mg?from=suggest_product
RGB LED 5mA R - 1,88V R = 224 Om G - 2,48V R = 104 Om B - 2,68V R = 64 Om

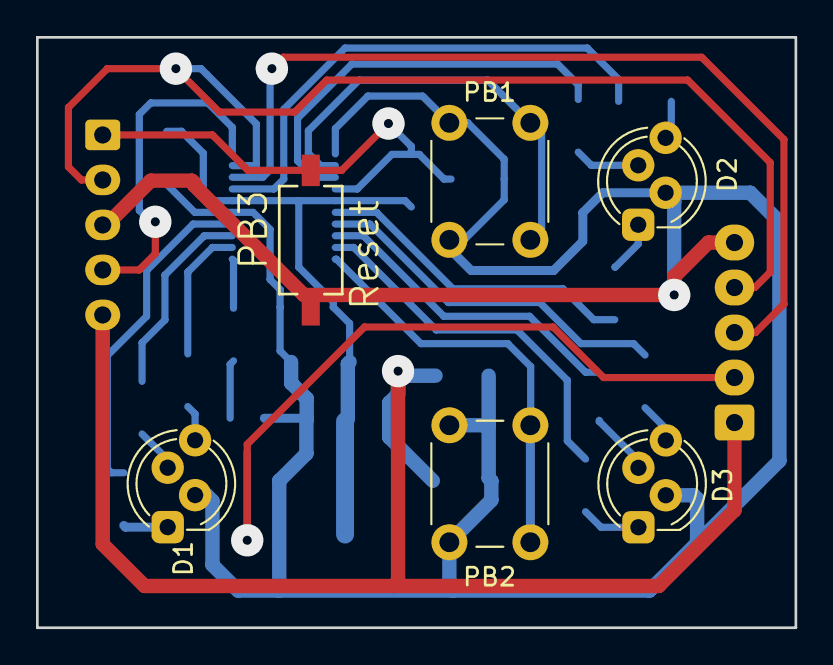
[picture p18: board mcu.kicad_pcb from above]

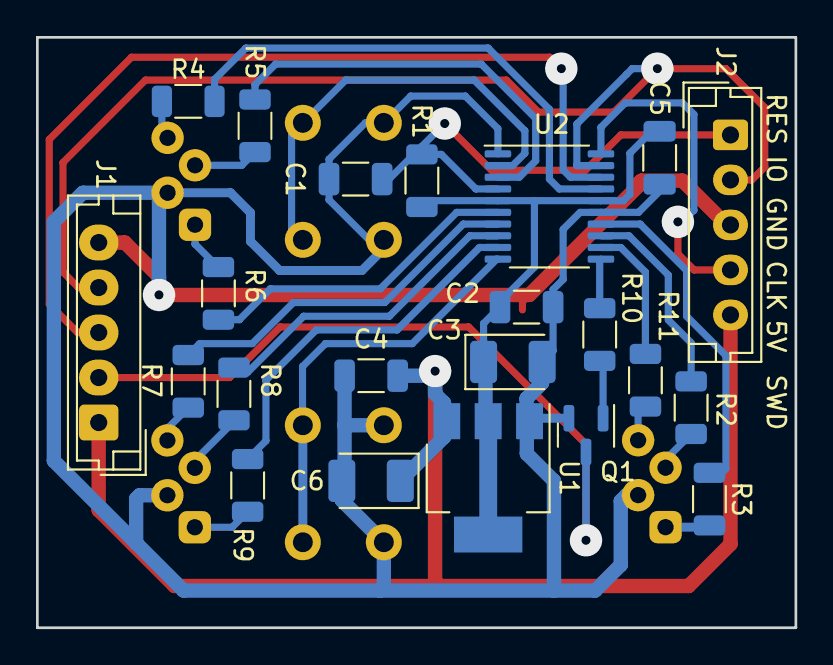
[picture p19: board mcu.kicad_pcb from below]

Board: 2 copper layers, 42.1 x 32.8 mm, 28 parts (22 on the bottom side), 30 nets.

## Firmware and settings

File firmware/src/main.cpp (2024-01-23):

#include "system/system.h"

// ----- main() ---------------------------------------------------------------

// Sample pragmas to cope with warnings. Please note the related line at
// the end of this function, used to pop the compiler diagnostics status.
#pragma GCC diagnostic push
#pragma GCC diagnostic ignored "-Wunused-parameter"
#pragma GCC diagnostic ignored "-Wmissing-declarations"
#pragma GCC diagnostic ignored "-Wreturn-type"

int
main(int argc, char* argv[])
{
	MCU::System.init();
	while(1){
		MCU::System.tick();
	}
}

#pragma GCC diagnostic pop

// ----------------------------------------------------------------------------

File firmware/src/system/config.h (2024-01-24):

#ifndef CONFIG_H
#define CONFIG_H

namespace MCU{

//--------------------------------------------------------------------------//
//                       Порты (ножки) микроконтроллера                     //
//--------------------------------------------------------------------------//
// Ножки RGB-светодиодов
constexpr int SENSOR1_LED_RED_PIN   = 6;
constexpr int SENSOR1_LED_GREEN_PIN = 3;
constexpr int SENSOR1_LED_BLUE_PIN  = 17;

constexpr int SENSOR2_LED_RED_PIN   = 9;
constexpr int SENSOR2_LED_GREEN_PIN = 8;
constexpr int SENSOR2_LED_BLUE_PIN  = 7;

constexpr int MAIN_LED_RED_PIN    = 14;
constexpr int MAIN_LED_GREEN_PIN  = 13;
constexpr int MAIN_LED_BLUE_PIN   = 12;

//--------------------------------------------------------------------------//
//                                 Выход на реле                            //
//--------------------------------------------------------------------------//
constexpr int RELAY_OUT_PIN    = 11;
constexpr int RELAY_HYSTERESIS = 1000; // 1 секунда
//--------------------------------------------------------------------------//
//                               Вход герконов                              //
//--------------------------------------------------------------------------//
constexpr int SENSOR1_PIN = 19;
constexpr int SENSOR2_PIN = 18;

//--------------------------------------------------------------------------//
//                                   Кнопки                                 //
//--------------------------------------------------------------------------//
constexpr int BUTTON1_PIN = 2;
constexpr int BUTTON2_PIN = 10;

//--------------------------------------------------------------------------//
//         Тайминги, для обработки аппаратных устройств (мкСек)             //
//--------------------------------------------------------------------------//
constexpr int MAIN_TIMER = 1000; // Период (мкСек) основного таймера устройства

// Все остальные тийминги будут опираться на MAIN_TIMER (делиться на него)
constexpr int RGB_LED_TIMER = 1000; // Период обработки RGB светодиода (частота 1кГц)
static_assert(RGB_LED_TIMER % MAIN_TIMER==0,"Должно кратно делиться на MAIN_TIMER");

constexpr int MAIN_LOOP_PERIOD = 10000; // Переодичность основного цикла. Думаю 100 раз в секунду - достаточно.
static_assert(MAIN_LOOP_PERIOD % MAIN_TIMER==0,"Должно кратно делиться на MAIN_TIMER");

constexpr int SENSORS_PERIOD = 10000; // Переодичность опроса сенсоров. Думаю 100 раз в секунду - достаточно.
static_assert(MAIN_LOOP_PERIOD % MAIN_TIMER==0,"Должно кратно делиться на MAIN_TIMER");

constexpr int BUTTONS_PERIOD = 10000; // Переодичность опроса кнопок. Думаю 100 раз в секунду - достаточно.
static_assert(MAIN_LOOP_PERIOD % MAIN_TIMER==0,"Должно кратно делиться на MAIN_TIMER");

constexpr int RELAY_PERIOD = 1000; // Переодичность опроса реле. 1мсек, чтобы гистерезис отрабатывать.
static_assert(MAIN_LOOP_PERIOD % MAIN_TIMER==0,"Должно кратно делиться на MAIN_TIMER");

}//namespace MCU

#endif // CONFIG_H

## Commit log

2024-01-05 Поробуем на плате разместить eeprom
    [mcu.kicad_pcb, mcu.kicad_sch]
2024-01-22 пока без eeprom
    [mcu.kicad_pcb, mcu.kicad_sch, power.kicad_pcb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]
2024-01-22 Немного каталоги перетусовал
    [mcu.kicad_pcb, mcu.kicad_sch]
2024-01-23 На питании диоды замкнул перемычками
    [power.kicad_pcb, power.kicad_sch]
2024-01-24 Забыл SWD 'выключить'
2024-01-24 Сенсоры перепутал-поправил. Усправил выход у Реле с OD на PP
    [mcu.kicad_pcb, mcu.kicad_sch]
2024-01-24 Добавил информаию по корпусу
    [front_panel.dxf, mcu.kicad_pcb, mcu.kicad_sch]
2024-01-25 Косметика
    [mcu.kicad_pcb, mcu.kicad_sch, power.kicad_pcb]
2024-01-29 add docs
    [mcu.kicad_pcb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]
2024-01-30 Вроде конец
2024-01-31 Детали, стоимость
    [mcu.csv, mcu.kicad_sch, power.csv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]
